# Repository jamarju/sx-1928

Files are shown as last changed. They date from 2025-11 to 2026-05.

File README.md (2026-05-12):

# SX-1928 alternative controller

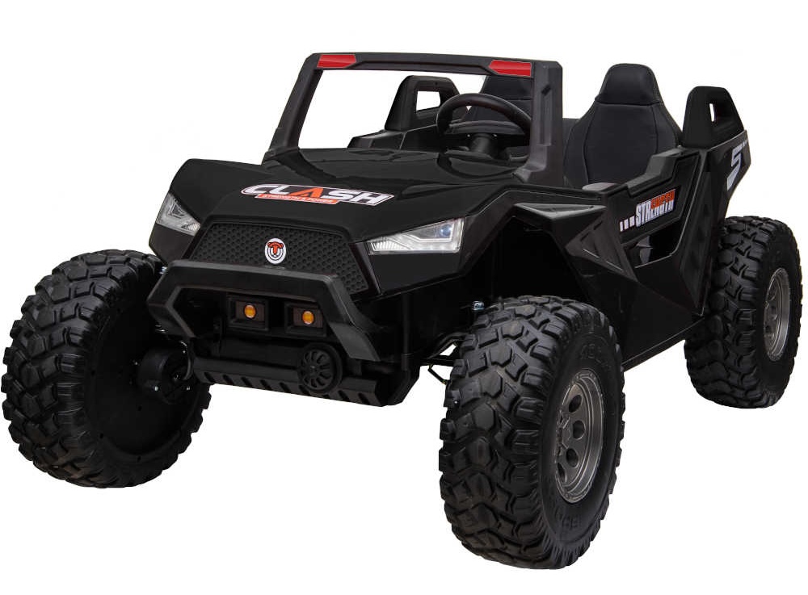
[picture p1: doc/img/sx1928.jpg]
SX-1928


Control board replacement for the SX-1928 ride-on car, aka "Clash" aka "Challenger" based on a **Futaba R617FS** and a **Robotdyn Mega 2560 Pro** Arduino board.

The original SX-1928 controller board had several shortcomings:

- **Limited speed control**: Only 2 fixed speed settings via on-board switch (or 3 from the RC transmitter)
- **Unsafe downhill speed**: Even the slowest setting is too fast on slopes
- **Sudden stops**: Car comes to a full stop too abruptly throwing children forward when releasing the pedal or the controller's throttle.
- **Poor steering control**: Basic on/off steering with no proportional control

I replaced the original controller with an Arduino Mega 2560 Pro and a Futaba R617FS receiver, and rewrote the firmware to fix the above issues and enhance the overall experience. Here are the main features:

- Fine-grained speed and steering control using the transmitter's analog sticks.
- Configurable acceleration/deceleration profiles prevent sudden speed changes.
- Kid/RC mode switching: the car can be controlled by the transmitter or by the kids using the pedal.
- Adjustable maximum pedal speed via the transmitter throttle stick.
- RC arming procedure prevents the car from moving unless authorized by the parent.

# Hardware Setup

- Receiver: Futaba R617FS (7-channel PWM output)
- Arduino: Robotdyn Mega 2560 Pro
- 100A DC motor drive module: https://aliexpress.com/item/1005005925917904.html
- 1x 24V 40A 4-pin automotive relay: https://www.amazon.es/dp/B0CJHQN6TY
- 1x 24V 40A 5-pin automotive relay: https://www.amazon.es/dp/B07MF5XJP9
- UBEC: Any 24V input, 5V output, 3A rated UBEC will do

Alternatively, 2x 24V 40A 5-pin relays can be used instead of 1x each.

# Electrical Setup

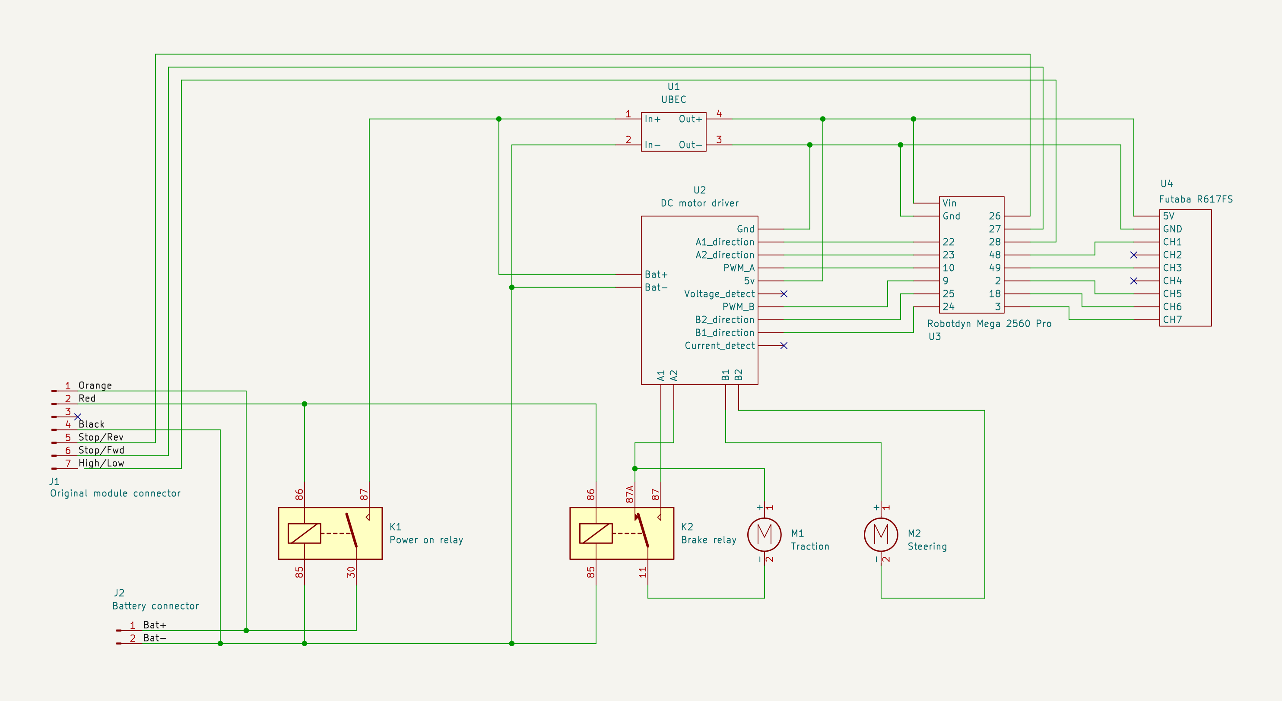
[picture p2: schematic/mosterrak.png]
Electrical Setup


# Pin Mapping

## Receiver Input Pins

| Receiver Channel | Function | Arduino Pin | Method | Signal Type | Range/Logic |
|---|---|---|---|---|---|
| **CH1** | Steering | **Pin 48**  | Input Capture | Analog | 1100-1900μs → 0-255 |
| **CH3** | Throttle | **Pin 49**  | Input Capture | Analog | 1100-1900μs → 255-0 (inverted) |
| **CH5** | Reverse | **Pin 2** | External Int | Digital | >1500μs = ON, ≤1500μs = OFF |
| **CH6** | Wired, ignored | **Pin 18**  | Not read | Analog | Unused |
| **CH7** | Takeover | **Pin 3** | External Int | Digital | ≤1500μs = ON, >1500μs = OFF |

## Motor Control Output Pins

### Drive Motor

| Function | Arduino Pin | AVR Pin | Timer/PWM | Notes |
|---|---|---|---|---|
| **A1** | **Pin 22** | PA0 | - | Direction control bit 1 (digital) |
| **A2** | **Pin 23** | PA1 | - | Direction control bit 2 (digital) |
| **PA_PWM** | **Pin 10** | PB4 | Timer2 OC2A | Motor speed PWM (~3.9kHz Phase Correct) |

## Steering Motor

| Function | Arduino Pin | AVR Pin | Timer/PWM | Notes |
|---|---|---|---|---|
| **B1** | **Pin 24** | PA2 | - | Direction control bit 1 (digital) |
| **B2** | **Pin 25** | PA3 | - | Direction control bit 2 (digital) |
| **PB_PWM** | **Pin 9** | PH6 | Timer2 OC2B | Steering PWM (~3.9kHz Phase Correct) |

## On-board Kid Controls

All switches are active-low: pins float when inactive and pull to GND when active, so they are read using digital inputs with internal pullups enabled. The direction switches (REV/FWD) and the speed selector are wired in series with the pedal, meaning the pedal must be pressed for them to register as active.

| Function | Arduino Pin | AVR Pin | Signal Type | Logic |
|---|---|---|---|---|
| **REV Pedal** | **Pin 26** | PA4 | Digital | LOW = reverse (active low) |
| **FWD Pedal** | **Pin 27** | PA5 | Digital | LOW = forward (active low) |
| **Speed Select** | **Pin 28** | PA6 | Digital | LOW = HI speed, HIGH = LO speed |

# TX configuration

This is the relevant configuration for the Futaba T7C transmitter.

- Hold `Mode/Page` 
  - `E.POINT`
    - Select `CH1`. Move the right stick left and right to set the steering end points between 1100 and 1900μs. Eg. left: 127%, right: 116%.
    - Select `CH3`. Move the left stick up and down to set the throttle end points between 1100 and 1900μs. Eg. up: 128%, down: 117%.
  - `REVERSE`: set all channels to normal `NOR`.
  - `TH-CUT`: you can assign one of the switches to cut the throttle to 0. Or just disable it by seeting it to `INH`.
  - `FAIL SAFE`: make throttle (CH3) go to 0 when the signal is lost: dial up to set `F/S`, then pull throttle stick down to 0, then push dial 1 sec to save the stick position as the failsafe position. Verify that it works by shutting down the transmitter and checking that the throttle goes to 0.

# Arming procedude

The car always starts in RC (remote control) mode and requires an arming sequence before it will respond to any controls:

1. **Power on transmitter** - Turn on the TX first
2. **Take control** - Switch B up (RC/takeover mode)
3. **Forward mode** - Switch G forward 
4. **Zero throttle** - Pull throttle stick fully down to 0
5. **Armed** - Car is now ready to drive

Once armed, you can control the car via RC or switch to kid control mode (Switch B down). The car will not move until this arming sequence is completed.

# State Machine

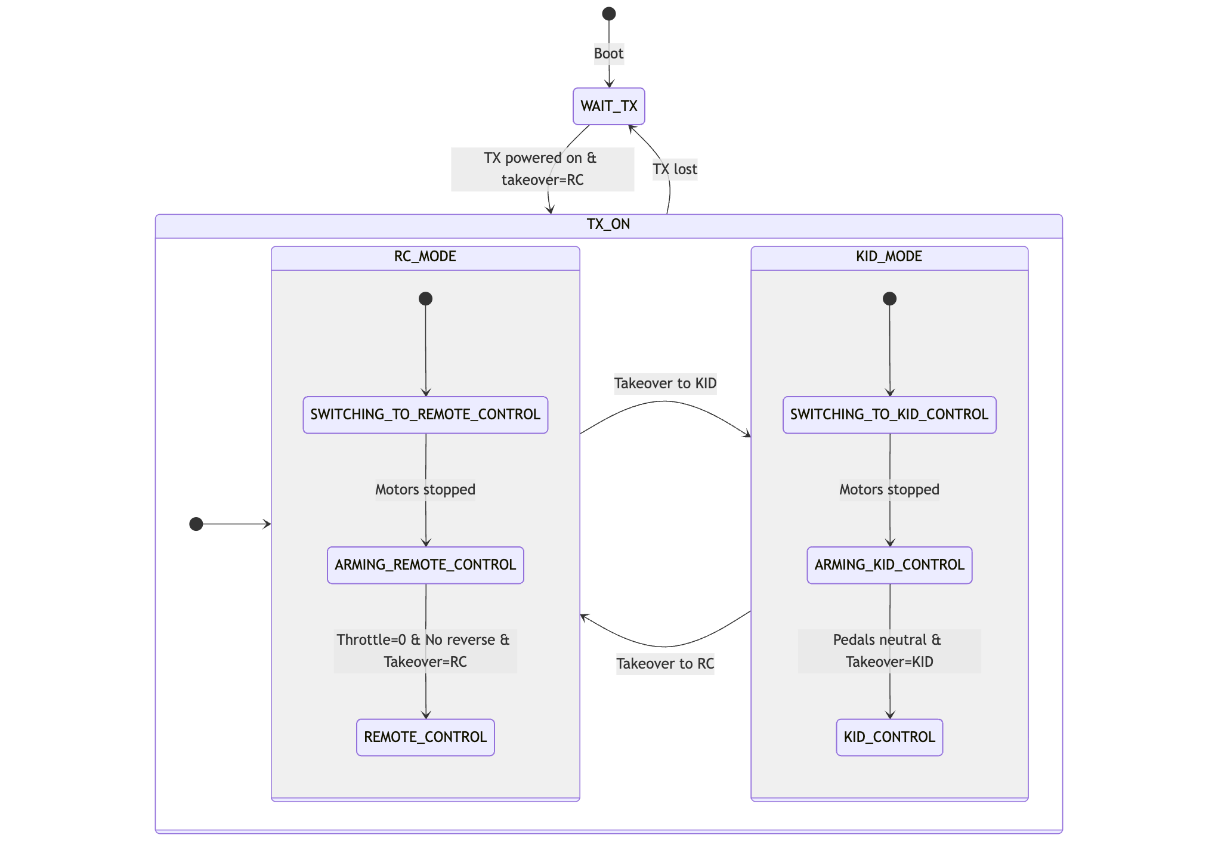
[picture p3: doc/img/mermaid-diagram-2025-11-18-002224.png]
State Machine


See [state_machine.md](doc/state_machine.md) for the state machine diagram and descriptions.

# Safety features

- **Power relay**: the whole car is powered by a 24V 40A 5-pin automotive relay. Turning the switch off will cut power to the car entirely.
- **Power off back EMF brake**: another relay brakes the car by shorting the motor terminals when the power is turned off. 
  - Note the car does not have mechanical brakes! This is a simple electrical brake that uses the back EMF of the motors to brake the car and only works in relatively flat terrain.
- **Acceleration**: motors ramp up linearly to full speed in 5.0 seconds, and ramp down to 0 speed in 1.0 second to prevent passengers from being thrown forward/backward. Actual ramp rates are definable in `RAMP_UP_RATE` and `RAMP_DN_RATE`.
- **Reversing while moving**: if you accidentally or intentionally reverse while the car is moving, the car will first slow down to a full stop, then speed up in the opposite direction following the above acceleration profile.
- **Kid control disabled by default**: car starts in RC (takeover) mode after the TX is powered on and the arming sequence is completed. Only then can you switch to kid control mode turning switch B down.
- **Arming procedure**: the car won't move until the arming sequence is completed:
  - Turn switch B up to take over (RC mode).
  - Turn switch G forward (forward mode).
  - Pull throttle stick down to 0.
  - Arming is completed, now you can control the car with the transmitter or switch to kid control mode turning switch B down.
- **Signal loss**: the car stops if the receiver signal is lost. 
  - Note: fail-safe mode must be configured in the transmitter! See instructions above. 
  - Note: The Futaba T7C / R617FS pair don't have a way to notify signal loss. When configured in fail-safe mode, they will simply pull the throttle to 0 and all other channels keep their last value.
- **Steering dead zone**: the steering stick has a dead zone around the center position to prevent motor movement when the stick is in the center position.
- **Steering hold**: the steering motor operates at a speed proportional to the stick position, i.e., the car turns faster the more you move the stick. However, since the steering motor lacks endstop switches or position feedback, the motor switches to "hold" mode after 2 seconds to prevent overheating and mechanical stress. In hold mode, the motor uses only 5% PWM power to maintain position without generating excessive heat.

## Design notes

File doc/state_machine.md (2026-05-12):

# Mosterrak State Machine

This document describes the control state machine for the Mosterrak system.

## State Diagram

```mermaid
---
config:
  theme: 'default'
---
stateDiagram-v2
    [*] --> WAIT_TX: Boot
    
    WAIT_TX --> TX_ON: TX powered on & takeover=RC
    TX_ON --> WAIT_TX: TX lost

    state TX_ON {
        direction LR
        [*] --> RC_MODE
        
        RC_MODE --> KID_MODE: Takeover to KID
        KID_MODE --> RC_MODE: Takeover to RC

        state RC_MODE {
            [*] --> SWITCHING_TO_REMOTE_CONTROL
            SWITCHING_TO_REMOTE_CONTROL --> ARMING_REMOTE_CONTROL: Motors stopped
            ARMING_REMOTE_CONTROL --> REMOTE_CONTROL: Throttle=0 & No reverse & Takeover=RC
        }

        state KID_MODE {
            [*] --> SWITCHING_TO_KID_CONTROL
            SWITCHING_TO_KID_CONTROL --> ARMING_KID_CONTROL: Motors stopped
            ARMING_KID_CONTROL --> KID_CONTROL: Pedals neutral & Takeover=KID
        }
    }
```

## State Descriptions

### WAIT_TX
- **Purpose**: Initial safe state, waiting for TX to be powered on. Motors are stopped and system is waiting for all 4 PWM channels to become active.
- **Previous state/s**: 
  - Boot (initial state)
  - Any state (when TX signal is lost)
- **Transitions**:
  - TX powered on (all 4 channels active) → `ARMING_REMOTE_CONTROL`

### ARMING_REMOTE_CONTROL
- **Purpose**: Safety check before entering RC control mode. System waits for operator to set safe input conditions (throttle at zero, no reverse) before allowing RC control. Car always boots into this mode for safety.
- **Previous state/s**:
  - `WAIT_TX` (when TX powers on)
  - `SWITCHING_TO_REMOTE_CONTROL` (when motors fully stopped)
- **Transitions**:
  - Throttle == 0 AND reverse switch OFF AND motors stopped AND takeover switch == RC → `REMOTE_CONTROL`
  - Takeover switch changed to KID → `SWITCHING_TO_KID_CONTROL`
  - TX signal lost → `WAIT_TX`

### ARMING_KID_CONTROL
- **Purpose**: Safety check before entering kid control mode. System waits for both pedals to be in neutral position before allowing kid control.
- **Previous state/s**:
  - `SWITCHING_TO_KID_CONTROL` (when motors fully stopped)
- **Transitions**:
  - Forward pedal OFF AND reverse pedal OFF AND motors stopped AND takeover switch == KID → `KID_CONTROL`
  - Takeover switch changed to RC → `SWITCHING_TO_REMOTE_CONTROL`
  - TX signal lost → `WAIT_TX`

### SWITCHING_TO_REMOTE_CONTROL
- **Purpose**: Safe transition to RC mode by ramping motors down to zero first. Prevents sudden motor behavior when switching modes.
- **Previous state/s**:
  - `KID_CONTROL` (takeover switch changed to RC)
  - `ARMING_KID_CONTROL` (takeover switch changed to RC)
  - `SWITCHING_TO_KID_CONTROL` (takeover switch changed back to RC)
- **Transitions**:
  - Motors fully stopped (ramped_speed == 0) → `ARMING_REMOTE_CONTROL`
  - Takeover switch changed to KID → `SWITCHING_TO_KID_CONTROL`
  - TX signal lost → `WAIT_TX`

### SWITCHING_TO_KID_CONTROL
- **Purpose**: Safe transition to kid mode by ramping motors down to zero first. Prevents sudden motor behavior when switching modes.
- **Previous state/s**:
  - `REMOTE_CONTROL` (takeover switch changed to KID)
  - `ARMING_REMOTE_CONTROL` (takeover switch changed to KID)
  - `SWITCHING_TO_REMOTE_CONTROL` (takeover switch changed back to KID)
- **Transitions**:
  - Motors fully stopped (ramped_speed == 0) → `ARMING_KID_CONTROL`
  - Takeover switch changed to RC → `SWITCHING_TO_REMOTE_CONTROL`
  - TX signal lost → `WAIT_TX`

### REMOTE_CONTROL
- **Purpose**: Active RC control operation. Operator has full control of throttle, reverse, and steering via the RC transmitter.
- **Previous state/s**:
  - `ARMING_REMOTE_CONTROL` (successfully armed)
- **Transitions**:
  - Takeover switch changed to KID → `SWITCHING_TO_KID_CONTROL`
  - TX signal lost → `WAIT_TX`

### KID_CONTROL
- **Purpose**: Active kid control operation. Kid has control via pedals (FWD/REV) and speed selector. Steering is controlled by RC transmitter (allows parent to steer). The RC throttle stick sets the maximum pedal speed, so pulling the throttle down commands zero speed.
- **Previous state/s**:
  - `ARMING_KID_CONTROL` (successfully armed)
- **Transitions**:
  - Takeover switch changed to RC → `SWITCHING_TO_REMOTE_CONTROL`
  - TX signal lost → `WAIT_TX`

## Common Transitions (Highest Priority)

These transitions override all state-specific transitions:

1. **TX Loss** (checked first): Any state → `WAIT_TX`
   - Condition: Any of the 5 PWM channels times out (>100ms without signal edge)
   - Motors immediately begin ramping down to 0

2. **Takeover Change** (checked second): Most states → `SWITCHING_TO_*`
   - Condition: Takeover switch position changes from previous loop
   - Direction: RC mode → `SWITCHING_TO_REMOTE_CONTROL`, KID mode → `SWITCHING_TO_KID_CONTROL`
   - Exception: Not checked in `WAIT_TX` state

## Safety Features

1. **Always Boot to RC Mode**: Car always starts in `ARMING_REMOTE_CONTROL` for safety, regardless of takeover switch position
2. **PWM Timeout**: All 5 channels must be active (signal within 100ms) for TX to be considered "on"
3. **Motor Ramping**: State changes that stop motors use ramping for smooth deceleration
4. **Arming Required**: Both control modes require specific safe input conditions before activation
5. **Switching States**: Mode changes always go through switching states to stop motors first
6. **TX Loss Priority**: TX signal loss takes absolute priority and immediately starts shutdown sequence
7. **Mode Lock**: Arming states verify takeover switch position matches target mode before completing transition

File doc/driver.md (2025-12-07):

## Product notes

From: https://aliexpress.com/item/1005005925917904.html

**100A DC motor drive Module High Power motor governor speed Control Dual H-bridge power supply 12V~48V 36V 24V optocoupler isolation**

This module uses a 10M high-speed optocoupler to isolate the input signal, effectively preventing the interference signal of the drive board from interfering with the control board, making the system more stable and reliable.

This module can be used to drive general DC motors with a maximum current of up to 100A . It is unmatched by general integrated motor drives. Therefore, it is very suitable for robot competitions, chariot competitions, and Freescale competitions.

Of course, this motor drive module is also very suitable for novices who are learning motor control, because its control method is very simple, see the following description for details

Features of drive module:

1. The basic components of the drive module body are patches, high integration, well-designed board layout, very beautiful, small size, onboard two high-power DC motor drive, the size of the drive module is only 80mm*70mm;
2. The large heat sink can effectively dissipate heat for the drive module when the current is large, and maintain the stable performance of the module;
3. When driving the motor, the maximum rated current of the module can reach 100A and the on-resistance is only 0.0015 ohm;
4. The switching frequency is high, up to 60KHZ, which effectively avoids the unpleasantness caused by the low frequency of the commissioning motor;
5. The control interface is very simple:
   - When A1.A2=0.0, it is brake;
   - When A1.A2=1.0, it is forward rotation;
   - A1.A2=0.1 is reverse;
   - PA is PWM wave input (motor speed adjustment);
   - G is the common ground pin with the control board (B road is the same control);
6. Both 3.3V and 5V microcontrollers can control this module, and only one motor power supply (12V~48V)

Driver board wiring diagram

Driver board wiring diagram

## Notes from different seller

https://aliexpress.com/item/1005003370023227.html

Please read the description before order!

this product can not connect RC Receiver( remote control)!  The PWM signal requirement of our driver is that the frequency is above 10K, and the duty cycle is 0-98% (the PWM frequency of the general aeromodelling controller is below 1K)

Because different customers have different use conditions, we usually recommend that the 100A drive board use a single channel with power below 500W (continuous). If it exceeds 500W, the heat dissipation capacity of the drive plate may not keep up with that of the drive plate. Generally, the greater the current, the greater the heat on the main circuit, and the higher the temperature rise. At this time, the temperature exceeds the solder melting point on the drive plate, which is easy to burn.

On the other hand, the heating of the drive plate is related to the load and the frequency of the drive signal. The switch tube operates in the hard switching mode, and the higher the frequency, the easier the heating. At the same time, if the load is reactive (capacitive or inductive load), the higher the temperature (switch loss) will be. These are all need to be carefully considered when selecting the drive plate. It is better to leave enough margin, instead of selecting the 100A drive plate for the 100A load.

other note:

The reverse electromotive force of the inductive load. If the current is large, the load will impact the switch tube of the drive board. Although there is TVS tube protection, if the load of the TVS tube is exceeded, the TVS tube will also be broken down (failure) and finally the switch tube will be broken down (at this time, the drive board will be burned!) These are related to the current size and load If you mind, please do not buy.

## My notes:

- The driver hates 100% PWM duty cycle, it will drop to ~0 volts output. So I limit the max speed to 254.
- I think that limit should be even lower at higher PWM frequencies, ej ~31.4 KHz (16 MHz / 510). So I prescaled the PWM to 8 for 3.92 KHz.
- A1=A2=PA=1 is hi-Z mode.

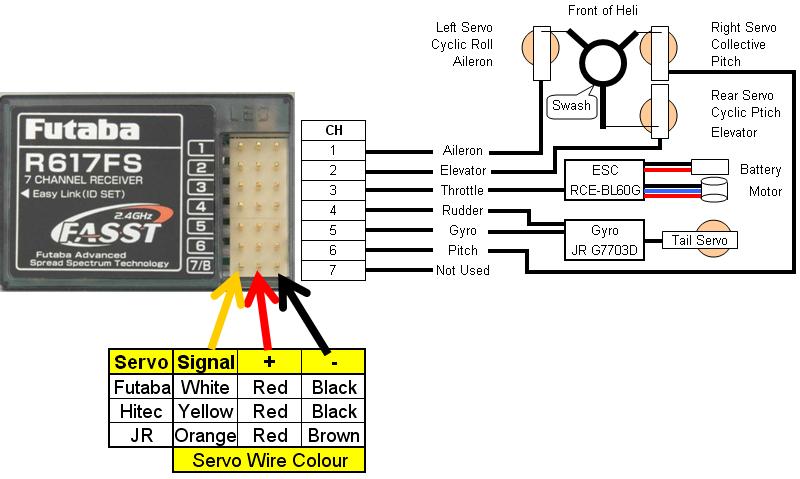
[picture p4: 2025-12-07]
doc/img/Futaba_R617FS_pinout.jpg

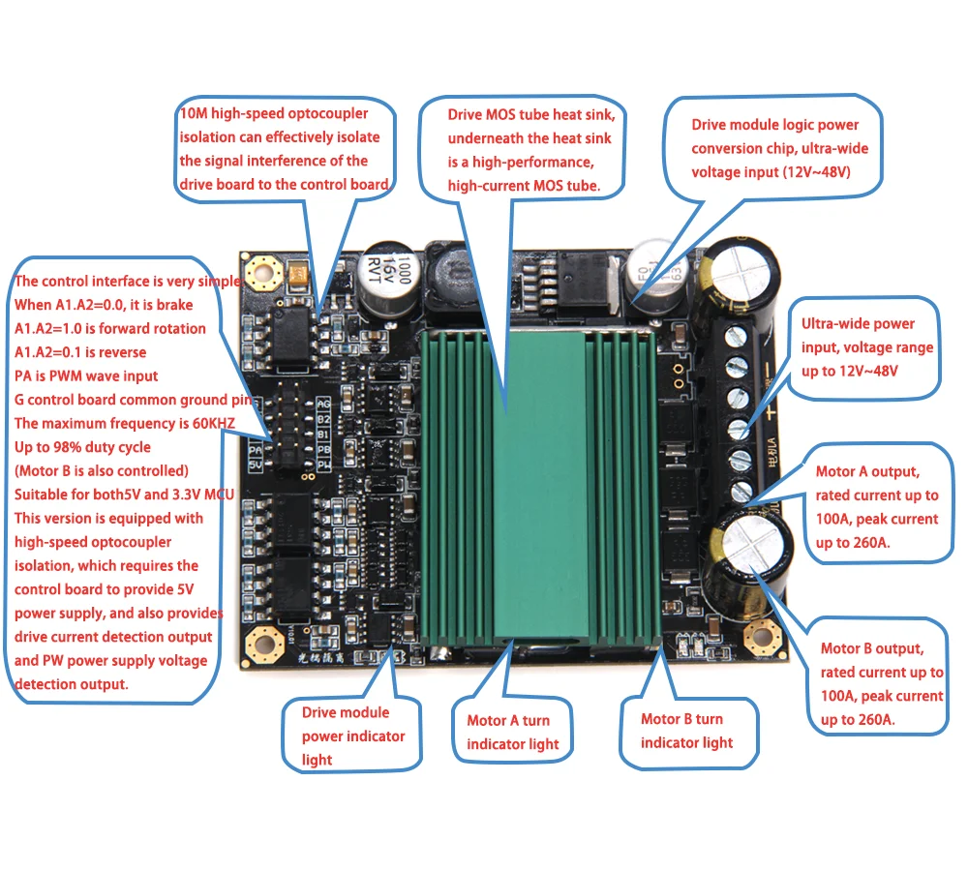
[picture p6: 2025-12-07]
doc/img/100A_driver_1.webp

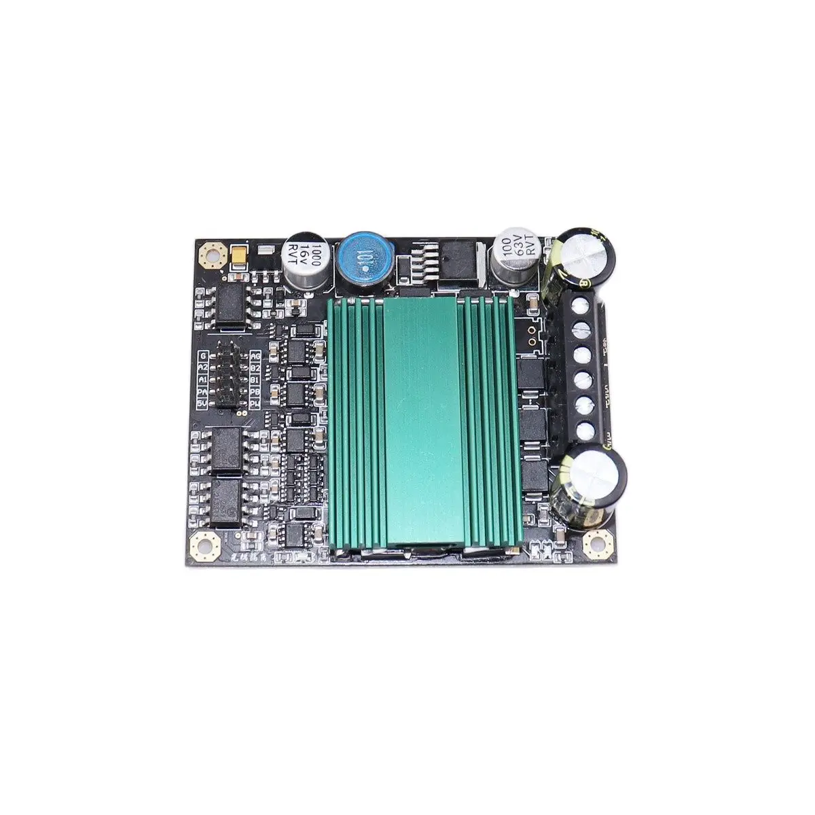
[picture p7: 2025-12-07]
doc/img/100A_driver_2.webp

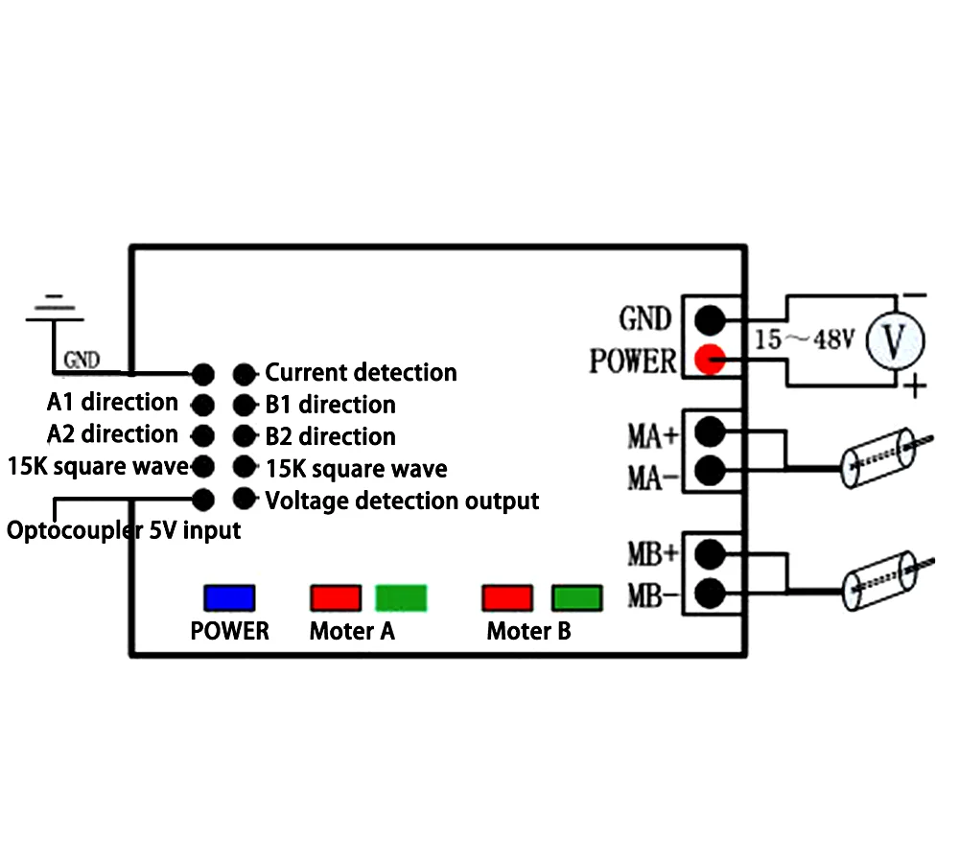
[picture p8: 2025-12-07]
doc/img/100A_driver_0.webp

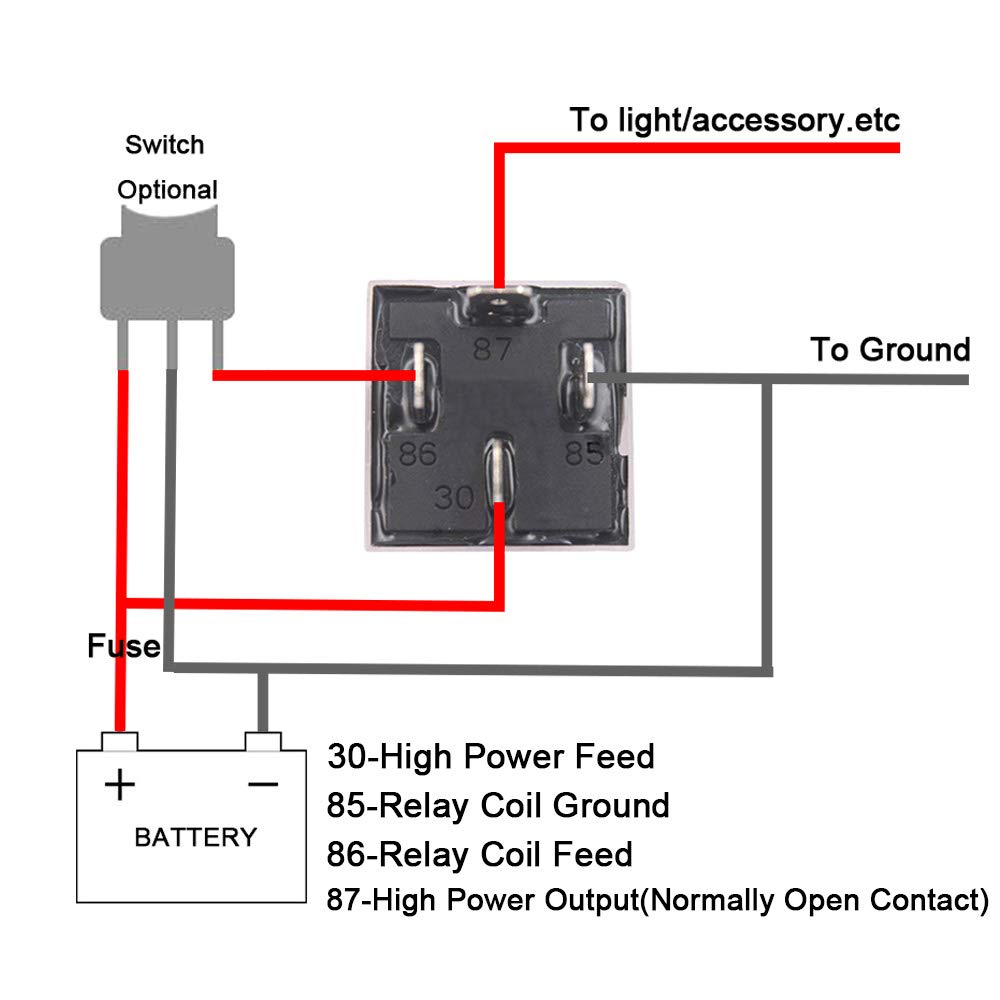
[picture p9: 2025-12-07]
doc/img/QitinDasen_61T0w.jpg

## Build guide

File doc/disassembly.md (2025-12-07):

# Trunk disassembly

Unscrew:

- 4 dashboard top screws
- 3 dashboard bottom screws (at an angle facing the driver)
- 2 dashboard side screws (embedded in the sides)
- 1 steering wheel screw

The trunk cover has clips all around the edges.

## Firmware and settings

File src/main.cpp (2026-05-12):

#include <Arduino.h>
#include <avr/wdt.h>
#include "receiver.h"
#include "motors.h"
#include "debug.h"
#include "main.h"
#include "onboard.h"
#include "version.h"

// Global state (non-static so debug.cpp can access)
ControlMode control_mode = WAIT_TX;         // Start in waiting for TX to be powered on
static bool last_takeover_state = false;    // Track takeover changes

// Disable watchdog at boot to prevent reset loop
void wdt_init(void) __attribute__((naked)) __attribute__((section(".init3")));
void wdt_init(void) {
  MCUSR = 0;
  wdt_disable();
}

void setup() {
  // Initialize debug serial output
  setup_debug();
  
  // Initialize the PWM receiver system
  setup_receiver();
  
  // Initialize motor control system  
  setup_motors();
  
  // Initialize onboard kid control hardware
  setup_onboard();
  
  // Enable watchdog timer - 500ms timeout
  // If loop() doesn't call wdt_reset() within 500ms, MCU will reset
  wdt_enable(WDTO_500MS);

  // Print firmware version
  Serial.print(FPSTR(MOSTERRAK_LOGO));
  Serial.println(FPSTR(VERSION_INFO_STR));
  Serial.println(F("Press 'h' for help"));
}

void loop() {
  wdt_reset();  // Pet the watchdog
  
  // Process debug commands
  process_debug_input();
  
  // Read all inputs
  bool tx_powered_on = is_tx_on();
  uint8_t steering = get_steering();
  uint8_t throttle = get_throttle();
  bool takeover_active = get_takeover();
  bool reverse_switch = get_reverse();
  uint8_t ramped_speed = get_ramped_speed();
  int16_t max_throttle = throttle;
  
  // Read onboard control states
  bool rev_pedal = get_rev_pedal();
  bool fwd_pedal = get_fwd_pedal();
  bool speed_low = get_speed_low();
  
  // Common state transitions (apply to all states)
  if (!tx_powered_on) {
    // Switch to WAIT_TX state if TX loss, this gets top priority
    control_mode = WAIT_TX;
  } else if (takeover_active != last_takeover_state) {
    // Switch to RC or KID control mode if takeover changed
    last_takeover_state = takeover_active;
    control_mode = takeover_active ? SWITCHING_TO_REMOTE_CONTROL : SWITCHING_TO_KID_CONTROL;
  }
  
  // Control state machine - each case handles its own state transitions
  switch (control_mode) {
    case WAIT_TX:
      ramp_motors(0);
      if (tx_powered_on && takeover_active) {
        control_mode = ARMING_REMOTE_CONTROL;
      }
      break;

    case SWITCHING_TO_REMOTE_CONTROL:
      ramp_motors(0);
      if (ramped_speed == 0) {
        control_mode = ARMING_REMOTE_CONTROL;
      }
      break;

    case SWITCHING_TO_KID_CONTROL:
      ramp_motors(0);
      if (ramped_speed == 0) {
        control_mode = ARMING_KID_CONTROL;
      }
      break;

    case ARMING_REMOTE_CONTROL:
      ramp_motors(0);
      if (throttle == 0 && ramped_speed == 0 && !reverse_switch) {
        control_mode = REMOTE_CONTROL;
      }
      break;

    case ARMING_KID_CONTROL:
      ramp_motors(0);
      if (!rev_pedal && !fwd_pedal && ramped_speed == 0) {
        control_mode = KID_CONTROL;
      }
      break;

    case REMOTE_CONTROL: {
      int16_t throttle_sign = reverse_switch ? -1 : 1;
      ramp_motors(throttle * throttle_sign);
      update_steering(steering);
      break;
    }

    case KID_CONTROL:
      update_steering(steering);
      if (!fwd_pedal && !rev_pedal) ramp_motors(0);
      else if (fwd_pedal && speed_low) ramp_motors(max_throttle / 2);
      else if (fwd_pedal && !speed_low) ramp_motors(max_throttle);
      else if (!fwd_pedal && speed_low) ramp_motors(-max_throttle / 2);
      else if (!fwd_pedal && !speed_low) ramp_motors(-max_throttle);
      break;
  }
  
  // Debug output
  print_debug_status();
}

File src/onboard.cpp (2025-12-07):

#include "onboard.h"

// Kid control hardware pins (with internal pullups)
static const uint8_t PIN_REV_PEDAL = 26;    // LOW = REV + pedal pressed
static const uint8_t PIN_FWD_PEDAL = 27;    // LOW = FWD + pedal pressed
static const uint8_t PIN_SPEED_LOW = 28;    // LOW = HI speed, HIGH = LO speed

void setup_onboard() {
  // Initialize kid control input pins with pullups
  pinMode(PIN_REV_PEDAL, INPUT_PULLUP);
  pinMode(PIN_FWD_PEDAL, INPUT_PULLUP);
  pinMode(PIN_SPEED_LOW, INPUT_PULLUP);
}

bool get_rev_pedal() {
  return !digitalRead(PIN_REV_PEDAL);  // Active LOW
}

bool get_fwd_pedal() {
  return !digitalRead(PIN_FWD_PEDAL);  // Active LOW
}

bool get_speed_low() {
  return !digitalRead(PIN_SPEED_LOW);  // Active LOW
}

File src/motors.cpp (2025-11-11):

#include "motors.h"
#include <avr/io.h>

// Drive motor control pin assignments
// Direction control: A1=0,A2=0 (brake), A1=1,A2=0 (fwd), A1=0,A2=1 (rev)
static const uint8_t A1_PIN = 22;            // PA0 - Direction control bit 1
static const uint8_t A2_PIN = 23;            // PA1 - Direction control bit 2
static const uint8_t PA_PWM_PIN = 10;        // Timer2 OC2A - PWM speed control

// Steering motor control pin assignments
// Direction control: B1=0,B2=0 (brake), B1=1,B2=0 (right), B1=0,B2=1 (left)
static const uint8_t B1_PIN = 24;            // PA2 - Direction control bit 1
static const uint8_t B2_PIN = 25;            // PA3 - Direction control bit 2
static const uint8_t PB_PWM_PIN = 9;         // Timer2 OC2B - PWM steering control

// Drive motor ramping constants (units per second)
// RAMP_UP_RATE: 0 to 255 in 5.0 seconds -> 255 / 5.0 = 51.0 units/sec
// RAMP_DN_RATE: 255 to 0 in 1.0 seconds -> 255 / 1.0 = 255.0 units/sec
static const float RAMP_UP_RATE = 51.0;
static const float RAMP_DN_RATE = 255.0;

// Drive motor ramping state
static float current_speed = 0.0;          // Current speed (0.0 to 255.0)
static unsigned long last_update_time = 0; // Last update timestamp in milliseconds

// Steering motor constants
static const uint8_t STEER_CENTER_VALUE = 128;     // Center position value
static const uint8_t STEER_DEADZONE = 16;          // Deadzone radius around center
static const uint8_t STEER_FULL_PWM = 254;         // Full power PWM (driver doesn't handle 255)
static const uint8_t STEER_HOLD_PWM = 13;          // Hold power PWM (~5%)
static const unsigned long STEER_HOLD_TIME = 2000; // Time before switching to hold (ms)

// Start of steering
static unsigned long steering_start_time = 0;

// Steering state machine
enum SteeringStickPosition {
  STEER_CENTER,
  STEER_LEFT,
  STEER_RIGHT,
};

static SteeringStickPosition prev_steer_state = STEER_CENTER;

void setup_motors() {
  // Configure drive motor control pins
  pinMode(A1_PIN, OUTPUT);
  pinMode(A2_PIN, OUTPUT); 
  pinMode(PA_PWM_PIN, OUTPUT);
  
  // Initialize to safe state (brake: A1=0, A2=0, PWM=0)
  digitalWrite(A1_PIN, LOW);
  digitalWrite(A2_PIN, LOW);
  
  // Setup Timer2 for Phase Correct PWM mode at ~3.9kHz (16MHz / (8 * 2 * 256))
  // Pin 10 = PB4 = OC2A (drive motor), Pin 9 = PH6 = OC2B (steering motor)
  
  // Configure Timer2 for Phase Correct PWM mode, prescaler 8
  TCCR2A = _BV(COM2A1) | _BV(COM2B1) | _BV(WGM20); // Phase Correct PWM mode, both OC2A and OC2B
  TCCR2B = _BV(CS21);  // Prescaler 8: CS22=0, CS21=1, CS20=0
  
  // Initialize PWM duty cycles to 0 (stopped)
  OCR2A = 0;  // PA_PWM_PIN (pin 10) - drive motor
  OCR2B = 0;  // PB_PWM_PIN (pin 9) - steering motor
  
  // Initialize ramping state
  current_speed = 0.0;
  last_update_time = millis();
  
  // Configure steering motor control pins
  pinMode(B1_PIN, OUTPUT);
  pinMode(B2_PIN, OUTPUT);
  pinMode(PB_PWM_PIN, OUTPUT);
  
  // Initialize steering to safe state (high-Z mode: B1=1, B2=1, PWM=255)
  disable_steering();
}

void ramp_motors(int16_t target_speed) {
  // Get elapsed time since last update
  unsigned long now = millis();
  unsigned long elapsed_ms = now - last_update_time;
  last_update_time = now;
  
  // Clamp to 254 max - driver doesn't handle 255 correctly
  if (target_speed < -254) target_speed = -254;
  if (target_speed > 254) target_speed = 254;

  // Convert target to float and calculate elapsed time in seconds
  float target_speed_f = (float)target_speed;
  float elapsed_sec = elapsed_ms / 1000.0;
  
  // Apply ramping
  if (current_speed < target_speed_f) {
    if (current_speed > 0) {
      // We are speeding up
      current_speed += RAMP_UP_RATE * elapsed_sec;
    } else {
      // We are slowing down
      current_speed += RAMP_DN_RATE * elapsed_sec;
    }
    if (current_speed > target_speed_f) {
      current_speed = target_speed_f;  // Clamp to target
    }
  }
  else if (current_speed > target_speed_f) {
    if (current_speed > 0) {
      // We are slowing down
      current_speed -= RAMP_DN_RATE * elapsed_sec;
    } else {
      // We are speeding up (in reverse)
      current_speed -= RAMP_UP_RATE * elapsed_sec;
    }
    if (current_speed < target_speed_f) {
      current_speed = target_speed_f;  // Clamp to target
    }
  }
  // else: already at target, no change needed
  
  // Apply to motors using the rounded ramped speed
  update_motors(get_ramped_speed());
}

uint16_t get_ramped_speed() {
  // Convert float speed to int16_t with rounding
  if (current_speed < 0) return (int16_t)(current_speed - 0.5);
  else return (int16_t)(current_speed + 0.5);
}

void disable_motors() {
  digitalWrite(A1_PIN, HIGH);
  digitalWrite(A2_PIN, HIGH);
  OCR2A = 255;
}

void update_motors(int16_t speed) {
  // Simply apply the requested speed and direction - no business logic
  
  if (speed == 0) {
    // Brake: A1=0, A2=0 (regardless of reverse flag)
    digitalWrite(A1_PIN, LOW);
    digitalWrite(A2_PIN, LOW);
    OCR2A = 0;
  }
  else if (speed < 0) {
    // Reverse: A1=0, A2=1
    digitalWrite(A1_PIN, LOW);
    digitalWrite(A2_PIN, HIGH);
    OCR2A = -speed;
  }
  else {
    // Forward: A1=1, A2=0
    digitalWrite(A1_PIN, HIGH);
    digitalWrite(A2_PIN, LOW);
    OCR2A = speed;
  }
}

void steer_right(uint8_t pwm_duty) {
  digitalWrite(B1_PIN, HIGH);
  digitalWrite(B2_PIN, LOW);
  OCR2B = pwm_duty;
}

void steer_left(uint8_t pwm_duty) {
  digitalWrite(B1_PIN, LOW);
  digitalWrite(B2_PIN, HIGH);
  OCR2B = pwm_duty;
}

void disable_steering() {
  digitalWrite(B1_PIN, HIGH);
  digitalWrite(B2_PIN, HIGH);
  OCR2B = 255;
}


void update_steering(uint8_t steering) {
  // Calculate deadzone boundaries
  uint8_t center_low = STEER_CENTER_VALUE - STEER_DEADZONE;
  uint8_t center_high = STEER_CENTER_VALUE + STEER_DEADZONE;
  SteeringStickPosition new_steer_state;

  if (steering < center_low) {
    new_steer_state = STEER_LEFT;
  } else if (steering >= center_high) {
    new_steer_state = STEER_RIGHT;
  } else {
    new_steer_state = STEER_CENTER;
  }

  if (new_steer_state != prev_steer_state) {
    prev_steer_state = new_steer_state;
    steering_start_time = millis();
  }

  switch (new_steer_state) {
    case STEER_CENTER:
      disable_steering();
      break;
    case STEER_LEFT:
      if (millis() - steering_start_time < STEER_HOLD_TIME) {
        steer_left(map(steering, center_low, 0, STEER_HOLD_PWM, STEER_FULL_PWM));
      } else {
        steer_left(STEER_HOLD_PWM);
      }
      break;
    case STEER_RIGHT:
      if (millis() - steering_start_time < STEER_HOLD_TIME) {
        steer_right(map(steering, center_high, 255, STEER_HOLD_PWM, STEER_FULL_PWM));
      } else {
        steer_right(STEER_HOLD_PWM);
      }
      break;
  }
}

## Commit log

2025-10-14 - CH7 (max throttle) in kid mode - refactor simplify steering code
2025-11-11 Stay in RC mode if car is turned on with TX off In this case the RX reads center for all channels, so the threshold is moved to include the center +/- some jitter/error.
    [receiver.cpp]
2025-12-07 Add electrical setup details, state machine documentation, and onboard control functionality
    - Updated README.md with electrical setup information and added sections for on-board kid controls and arming procedure.
    - Introduced state machine documentation for the Mosterrak system.
    - Added new files for trunk disassembly and driver module notes.
    - Implemented onboard control functions for kid pedals in onboard.cpp and onboard.h.
    - Enhanced debug output in debug.cpp to reflect current control mode and TX status.
    - Updated main control logic to handle new WAIT_TX state and improved takeover handling in main.cpp.
    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
2025-12-07 Add initial KiCad project files for Mosterrak
    - Created new KiCad PCB, schematic, symbol library, and project files for the Mosterrak project.
    - Included configuration files for board layout, schematic design, and symbol definitions.
    - Established a basic structure for the project to facilitate further development.
    [mosterrak.kicad_pcb, mosterrak.kicad_sch]
2025-12-07 Update .gitignore to include backup files and prevent clutter
    - Added entries to ignore Mosterrak schematic backup ZIP files and .bak files.
    - Ensured .DS_Store files are also ignored to maintain a clean repository.
2025-12-07 Enhance README.md with detailed features of the SX-1928 alternative controller
    - Updated the README.md to reflect the new project name and added a comprehensive list of improvements over the original SX-1928 controller.
    - Included a new image and detailed descriptions of enhanced speed and steering control, configurable profiles, and safety features for user experience.
2026-05-12 Use main throttle for kid speed limit
